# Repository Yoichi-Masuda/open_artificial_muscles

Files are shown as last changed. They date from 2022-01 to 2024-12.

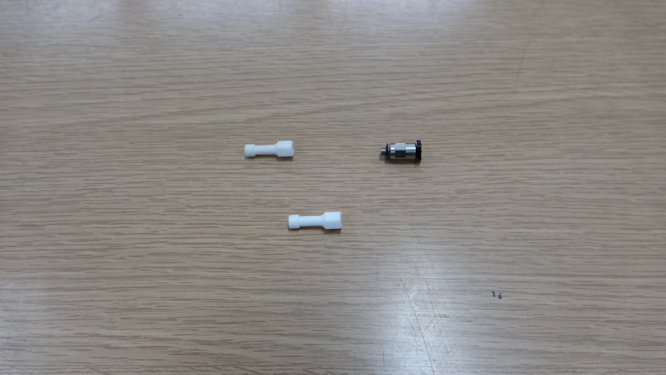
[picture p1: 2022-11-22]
thin_muscle/end_assembly1.JPG

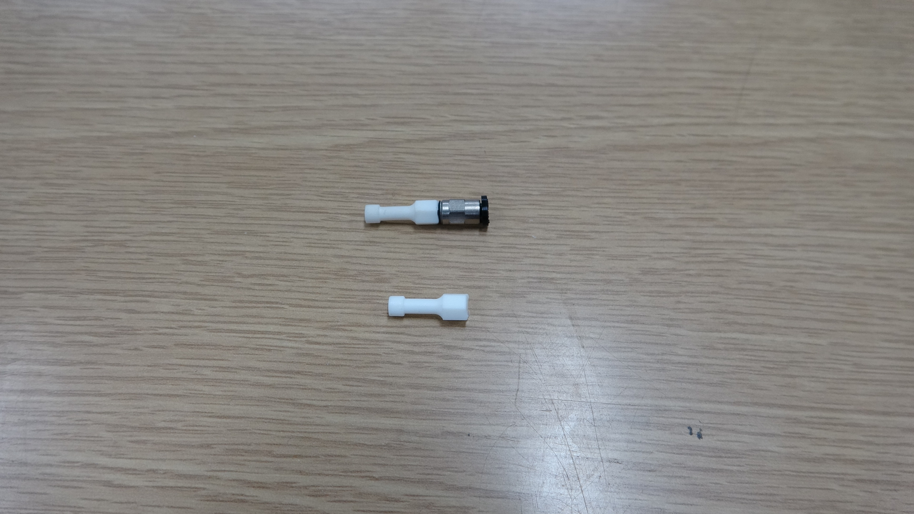
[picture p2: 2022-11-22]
thin_muscle/end_assembly2.JPG

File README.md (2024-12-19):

## マッキベン型人工筋肉　

[こちらのサイト](https://ishikawa-lab.sakura.ne.jp/yoichi/muscle_recipe)で公開しているマッキベン型人工筋肉（通称：Y式マッキベン）のレシピと３Dプリントファイルを公開しています．
径のラインナップは3種類あり，上記サイト内や動画で説明しているのは，外径が9mmの一番大きいものについてです．

7mmと5mmの動画はありませんが，おおよその作り方は変わりません．
収縮率は9mmが30％なのに対して，少し控えめの15％と10％なので注意してください．
これで物足りない方には、さらに高性能なs-muscle社の細径人工筋肉をオススメします！ https://s-muscle.com

<font color="red"> NEW!! Coro @corone422 さんの改良版5mmレシピを追加しました．収縮率は20％ほど，0.8MPaを入れられるそうです．（2022/12/03） </font>

全ての径に対して金属かしめが必要ですが，かしめ用の工具は
- [アポロホースカシメ工具](https://www.monotaro.com/p/8848/9344/)　2290円

が共通で使用可能です．

### 【人工筋の材料】外径9mm（収縮率30％ほど）

- デンカエレクトロン　ほつれにくい編組チューブ　[NFL-9](https://www.monotaro.com/p/3506/8223/)　1m 648円
- モノタロウ　シリコンチューブ　[MGJG-8×10（内径8mm，外形10mm）](https://www.monotaro.com/p/2225/2536/?t.q=%22MGJG-8%81~10%22)　1m 279円
- エスコ　9-11mm ホースクランプ(ツーイヤー型/10個)　 [EA463AE-11](https://www.monotaro.com/p/4993/6617/)　506円
- SMC　ストレート KQ2H ミリサイズ　[KQ2H04-00A](https://www.monotaro.com/p/4138/4786/)　318円
- タミヤ　タミヤセメント（ABS用）　ITEM 87137　278円　…※３Dプリント品の積層痕を消すため
- ３Dプリント品　ABS製の栓：[リンク](https://github.com/Yoichi-Masuda/Art_muscles/blob/master/air_stopper.stl)
    - 一般的な熱積層方式の３Dプリンタで造形可能
    空気圧の漏れを防ぐため，インフィルは100％が理想
    - 「ピスコ(PISCO)　プラグ　PP4」と「SMC　ストレート KQ2H ミリサイズ　KQ2H04-00A」の組み合わせでも代用可能

### 【人工筋の材料】外径7mm（収縮率15％ほど）

- デンカエレクトロン　ほつれにくい編組チューブ　[NFL-6](https://www.monotaro.com/p/3506/8187/)　1m 439円
- タイガースポリマー　シリコンチューブ　[SR1554（内径5mm，外形7mm）](https://www.monotaro.com/p/3278/8402/) 1m　249円
- エスコ　7-9mm ホースクランプ(ツーイヤー型/10個入り)　 [EA463AE-9](https://www.monotaro.com/p/4993/6748/)　395円 
- コガネイ　クイック継手ミニタイプ TSシリーズ ストレート [TS4-M5M](https://jp.misumi-ec.com/vona2/detail/221000065534/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) 単価188円

- 3Dプリント品
    - UV硬化レジン製の継手：[リンク](https://github.com/Yoichi-Masuda/open_artificial_muscles/blob/master/thin_muscle/coupler_M5.stl)
    - UV硬化レジン製の栓：[リンク](https://github.com/Yoichi-Masuda/open_artificial_muscles/blob/master/thin_muscle/cap_M5.stl)
        - 3Dプリント品の継手にはネジがモデリングされていますが，造形後にM5タップでネジをさらった方が簡単かつ，空気の漏れなく組み立てが可能です．
        - 7mmと5mmの人工筋のパーツのみ，光硬化式プリンタで造形する必要があります．レジンは[こちら](https://www.amazon.co.jp/dp/B09H2XZTSK)を推奨します．

### 【人工筋の材料】外径5mm（収縮率10％ほど）

- デンカエレクトロン　ほつれにくい編組チューブ　[NFL-3](https://www.monotaro.com/p/3506/8144/)　1m 359円
- タイガースポリマー　シリコンチューブ　[SR1554（内径3mm，外形5mm）](https://www.monotaro.com/p/3278/8244/) 1m　179円
- エスコ　5-7mm ホースクランプ(ツーイヤー型/10個入り)　 [EA463AE-7](https://www.monotaro.com/p/4993/6732/)　395円 
- コガネイ　クイック継手ミニタイプ TSシリーズ ストレート [TS3-M3M](https://jp.misumi-ec.com/vona2/detail/221000065534/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) 単価195円

- 3Dプリント品
    - UV硬化レジン製の継手：[リンク](https://github.com/Yoichi-Masuda/open_artificial_muscles/blob/master/thin_muscle/coupler_M3.stl)
    - UV硬化レジン製の栓：[リンク](https://github.com/Yoichi-Masuda/open_artificial_muscles/blob/master/thin_muscle/cap_M3.stl)
        - 3Dプリント品の継手にはネジがモデリングされていますが，造形後にM3タップでネジをさらった方が簡単かつ，空気の漏れなく組み立てが可能です．造形時に空気穴が塞がってしまうことがありますが，Φ1mmのドリルで追加工して使用することが可能です．
        - 7mmと5mmの人工筋のパーツのみ，光硬化式プリンタで造形する必要があります．レジンは[こちら](https://www.amazon.co.jp/dp/B09H2XZTSK)を推奨します．

外径5mmの人工筋は，接続するエアチューブ（ポリウレタンチューブ）の外径が3mmであることに注意してください（[外径3mmのポリウレタンチューブの例](https://www.monotaro.com/p/5815/5517/) 1mあたり約40円程度）

### 3Dプリント品とクイック継手の接続

外径7mm,外径5mmの人工筋は，製作前に3Dプリント品のネジにクイック継手をあらかじめ接続しておきます（写真参照）．このことに加え，栓にABS用の接着剤が不要であること以外は，動画でも説明されている外径9mmの人工筋の製法と同様です．



### 径ごとの性能差

上記のラインナップのうち，外径が5mmの最小のものについては，他の人工筋に比べて収縮率が低くなっています．編組チューブの編み方やシリコンチューブの厚みによって，収縮率は変化するため，異なる製品や厚みでの細径人工筋の検討を我々も行っています．是非良い改善，検討案などがあればアドバイスいただけると幸いです．

## みなさんの改良版レシピ
### [@corone422](https://twitter.com/corone422/status/1598710760959782912?s=20&t=0VL1ZC6_-5MBRaOd5uCATQ)さんの細径マッキベン（外形5mm）
[@corone422](https://twitter.com/corone422/status/1598710760959782912?s=20&t=0VL1ZC6_-5MBRaOd5uCATQ)さんが5mmマッキベンのレシピを改良してくださいました．収縮率は20％ほどだそうです．
動作中の様子は[こちら](https://twitter.com/corone422/status/1587334103325880320?s=20&t=0VL1ZC6_-5MBRaOd5uCATQ)．



> Coro @corone422 [午前1:56 · 2022年12月3日](https://twitter.com/corone422/status/1598722900210900992?s=20&t=0VL1ZC6_-5MBRaOd5uCATQ)
> - スリーブは https://monotaro.com/p/3506/8205/
> - シリコンチューブは https://monotaro.com/p/3473/9336/
> - カシメは https://monotaro.com/g/02398866/
> 
> それで従来のレシピですとストレートをジョイントに使っていますが、改良した方はシリコンホースそのものを埋め込みました。止栓は光造形で直径4mmの棒を作りました。【続く】

> Coro @corone422 [午前10:45 · 2022年12月3日](https://twitter.com/corone422/status/1598855958742306816?s=20&t=0VL1ZC6_-5MBRaOd5uCATQ)
> シリコンチューブとポリウレタンチューブの摩擦を利用してうまく止まっているような感じになりますね。なのでカシメの時にひらべったく潰れちゃうので、耳と耳を工具で挟み、チューブを丸く戻し> > てあげる作業だけ必要になってきます。

チューブがつぶれないように、[インサートリング](https://www.monotaro.com/p/3531/4526/?t.q=%83C%83%93%83T%81%5B%83g%83%8A%83%93%83O)を入れればいいかもしれません．
締結力も上がるはず．

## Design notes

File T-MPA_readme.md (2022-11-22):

## マッキベン型人工筋肉　

今回の目玉です．
径のラインナップは3種類あり，動画で説明しているのは，外径が9mmの一番大きいものについてです．

全ての径に対して金属かしめが必要ですが，かしめ用の工具は
- [アポロホースカシメ工具](https://www.monotaro.com/p/8848/9344/)　2290円

が共通で使用可能です．

### 【人工筋の材料】外径9mm

- デンカエレクトロン　ほつれにくい編組チューブ　[NFL-9](https://www.monotaro.com/p/3506/8223/)　1m 648円
- タイガースポリマー　シリコンチューブ　[SR1554（内径7mm，外形9mm）](https://www.monotaro.com/p/3278/8603/)　1m 219円
- エスコ　9-11mm ホースクランプ(ツーイヤー型/10個)　 [EA463AE-11](https://www.monotaro.com/p/4993/6617/)　506円
- SMC　ストレート KQ2H ミリサイズ　[KQ2H04-00A](https://www.monotaro.com/p/4138/4786/)　318円
- タミヤ　タミヤセメント（ABS用）　ITEM 87137　278円　…※３Dプリント品の積層痕を消すため
- ３Dプリント品　ABS製の栓：[リンク](https://github.com/Yoichi-Masuda/Art_muscles/blob/master/air_stopper.stl)
    - 一般的な熱積層方式の３Dプリンタで造形可能
    空気圧の漏れを防ぐため，インフィルは100％が理想
    - 「ピスコ(PISCO)　プラグ　PP4」と「SMC　ストレート KQ2H ミリサイズ　KQ2H04-00A」の組み合わせでも代用可能

### 【人工筋の材料】外径7mm

- デンカエレクトロン　ほつれにくい編組チューブ　[NFL-6](https://www.monotaro.com/p/3506/8187/)　1m 439円
- タイガースポリマー　シリコンチューブ　[SR1554（内径5mm，外形7mm）](https://www.monotaro.com/p/3278/8402/) 1m　249円
- エスコ　7-9mm ホースクランプ(ツーイヤー型/10個入り)　 [EA463AE-9](https://www.monotaro.com/p/4993/6748/)　395円 
- コガネイ　クイック継手ミニタイプ TSシリーズ ストレート [TS4-M5M](https://jp.misumi-ec.com/vona2/detail/221000065534/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) 単価188円

- 3Dプリント品　UV硬化レジン製の継手：[リンク](githubのリンクM5)
            　UV硬化レジン製の栓：[リンク](githubのリンクM5)
3Dプリント品の継手にはネジがモデリングされていますが，造形後にM5タップでネジをさらった方が簡単かつ，空気の漏れなく組み立てが可能です．

### 【人工筋の材料】外径5mm

- デンカエレクトロン　ほつれにくい編組チューブ　[NFL-3](https://www.monotaro.com/p/3506/8144/)　1m 359円
- タイガースポリマー　シリコンチューブ　[SR1554（内径3mm，外形5mm）](https://www.monotaro.com/p/3278/8244/) 1m　179円
- エスコ　5-7mm ホースクランプ(ツーイヤー型/10個入り)　 [EA463AE-7](https://www.monotaro.com/p/4993/6732/)　395円 
- コガネイ　クイック継手ミニタイプ TSシリーズ ストレート [TS3-M3M](https://jp.misumi-ec.com/vona2/detail/221000065534/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) 単価195円

- 3Dプリント品　UV硬化レジン製の継手：[リンク](githubのリンクM3)
            　UV硬化レジン製の栓：[リンク](githubのリンクM3)
3Dプリント品の継手にはネジがモデリングされていますが，造形後にM3タップでネジをさらった方が簡単かつ，空気の漏れなく組み立てが可能です．造形時に空気穴が塞がってしまうことがありますが，Φ1mmのドリルで追加工して使用することが可能です．

外径5mmの人工筋は，接続するエアチューブ（ポリウレタンチューブ）の外径が3mmであることに注意してください．

[外径3mmのポリウレタンチューブの例](https://www.monotaro.com/p/5815/5517/) 1mあたり約40円程度

### 3Dプリント品とクイック継手の接続

外径7mm,外径5mmの人工筋は，製作前に3Dプリント品のネジにクイック継手をあらかじめ接続しておきます（写真参照(中間1.jpg,中間2.jpg,最小1.jpg,最小2.jpgあたりをご使用ください)）．このことに加え，栓にABS用の接着剤が不要であること以外は，動画でも説明されている外径9mmの人工筋の製法と同様です．

### 径ごとの性能差

上記のラインナップのうち，外径が5mmの最小のものについては，他の人工筋に比べて収縮率が低くなっています．編組チューブの編み方やシリコンチューブの厚みによって，収縮率は変化するため，異なる製品や厚みでの細径人工筋の検討を我々も行っています．是非良い改善，検討案などがあればアドバイスいただけると幸いです．

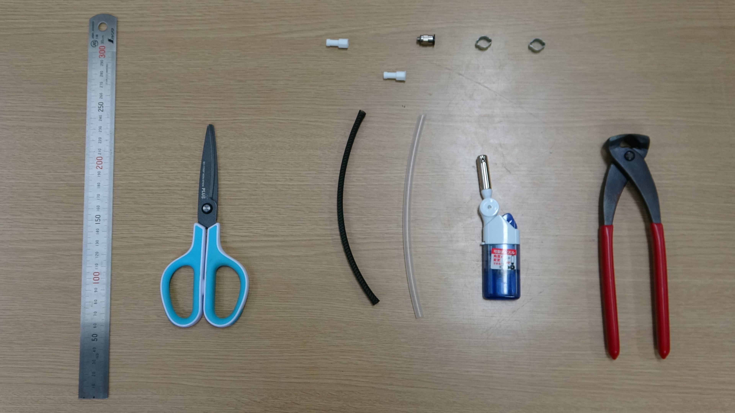
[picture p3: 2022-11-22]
thin_muscle/7mm_muscle.JPG

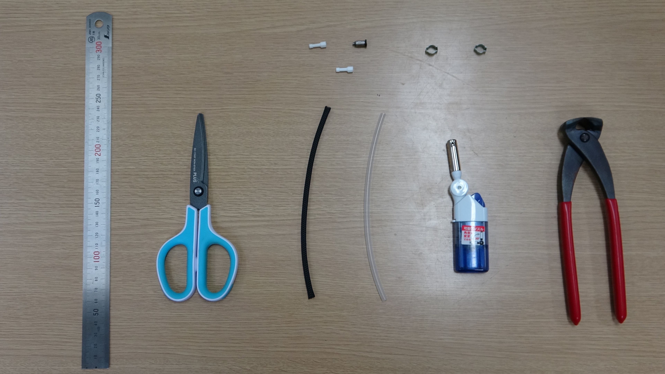
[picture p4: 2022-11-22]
thin_muscle/5mm_muscle.JPG

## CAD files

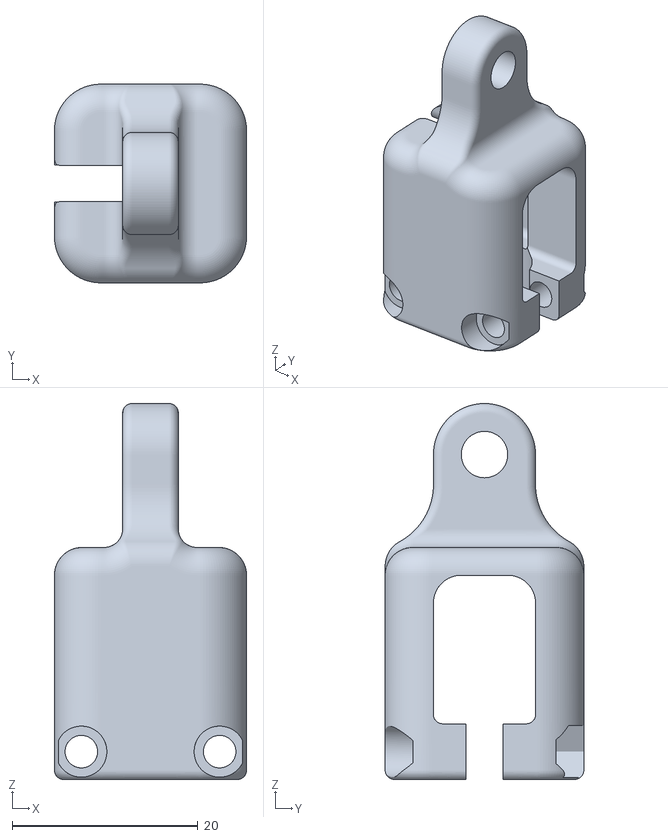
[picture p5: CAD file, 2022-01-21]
muscle_holder.stl
20.7 x 21.4 x 40.5

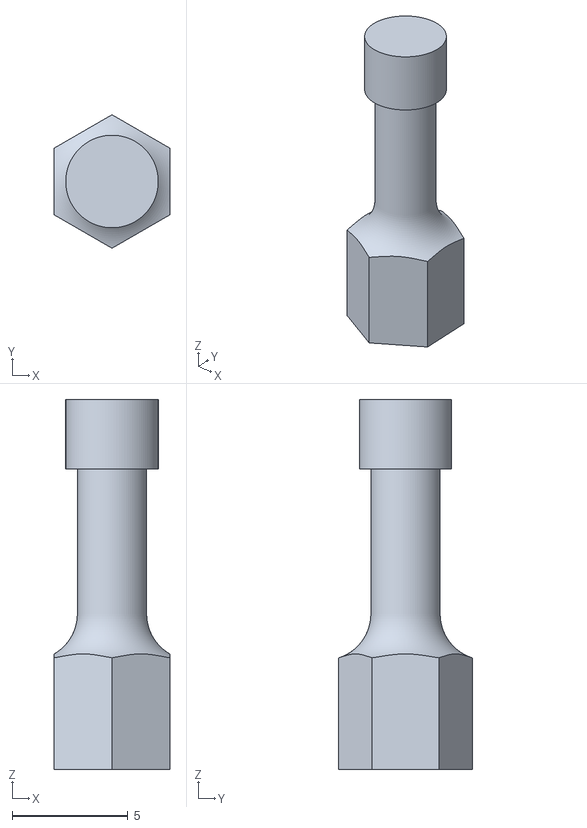
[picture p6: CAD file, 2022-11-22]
thin_muscle/cap_M3.stl
5.00 x 5.77 x 16.0

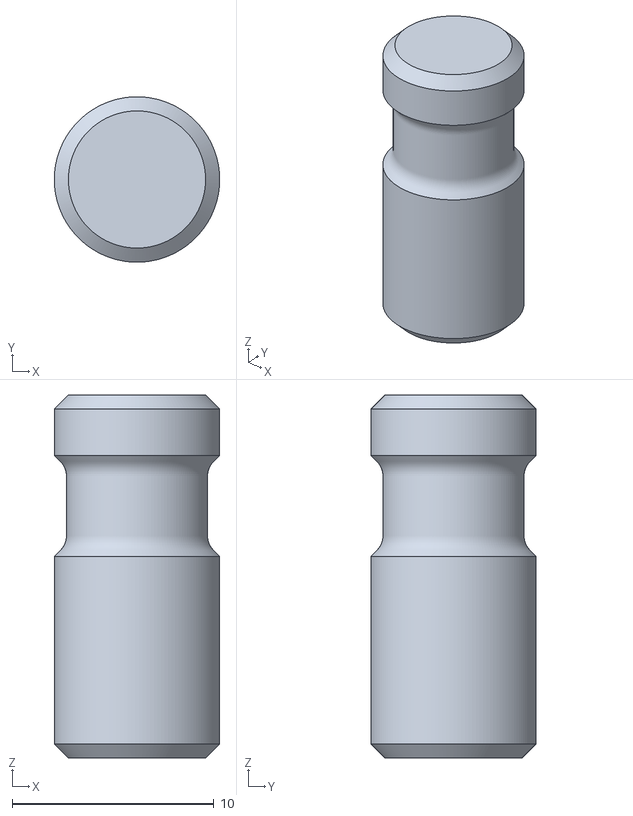
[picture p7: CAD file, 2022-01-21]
air_stopper.stl
8.20 x 8.20 x 18.0

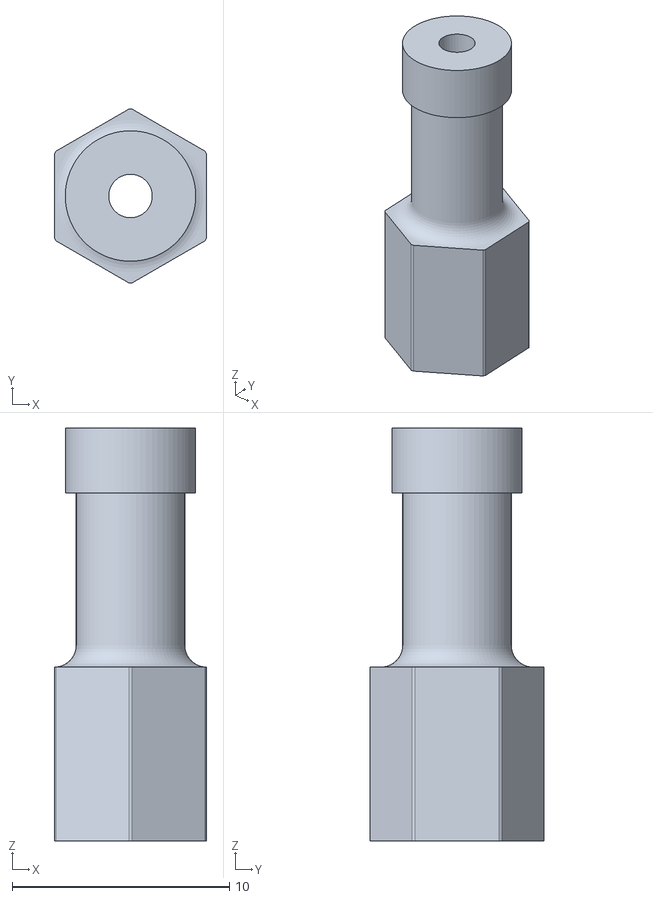
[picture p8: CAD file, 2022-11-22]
thin_muscle/coupler_M5.stl
7.00 x 8.00 x 19.0

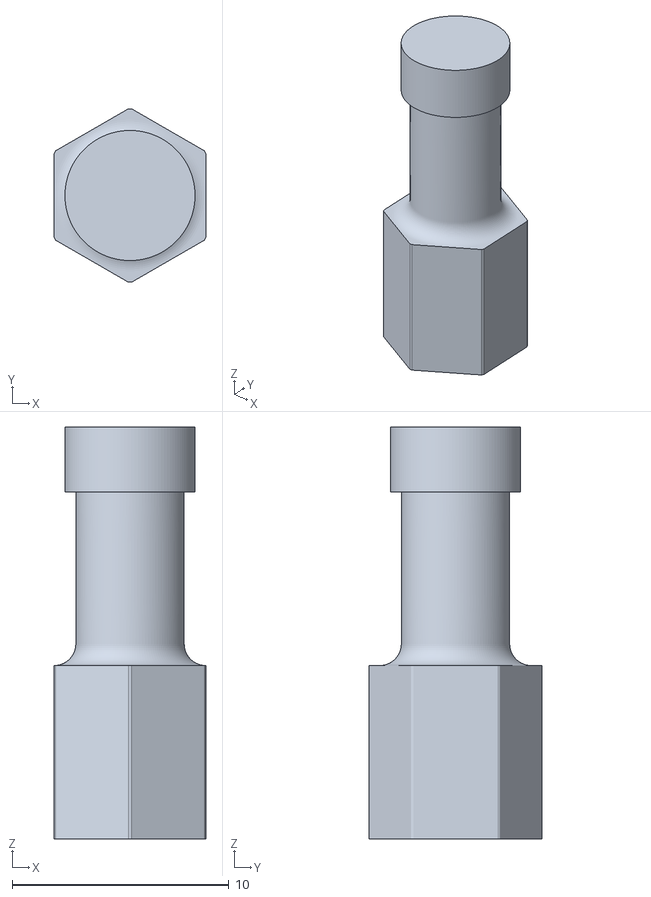
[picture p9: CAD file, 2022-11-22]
thin_muscle/cap_M5.stl
7.00 x 8.00 x 19.0

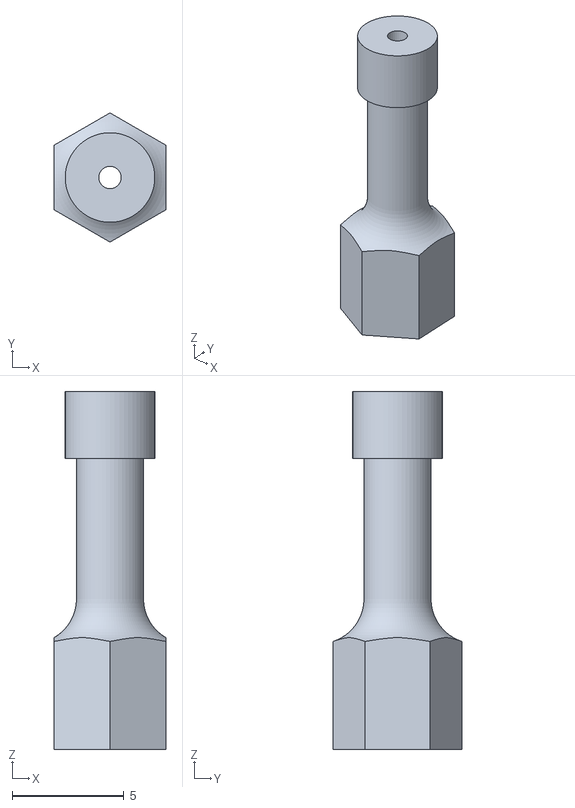
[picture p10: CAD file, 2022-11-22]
thin_muscle/coupler_M3.stl
5.00 x 5.77 x 16.0

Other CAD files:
air_stopper.ipt
muscle_holder.ipt
